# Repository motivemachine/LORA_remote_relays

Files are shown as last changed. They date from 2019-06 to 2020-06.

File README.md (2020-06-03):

# Lora Remote Relays

AC powered relay control board using Lora radios. Turn on lights, heaters or anything else you need at a distance.
The first one has been installed and running smooth for several months now! Check it out here: https://asthemillturns.serveblog.net/lora-ac-relays.html

## Notice about AC and relays!
##### Build at your own risk.
This devices runs on 110VAC, and controls other 110VAC devices. Do not make this if you don't know what you're doing! Power traces are very conservatively rated at 8 amp total (both relays combined), further changes and testing should increase this. There is no snubber circuity on the relays, so as-is should only be used with resistive loads (lights, heaters, etc.). Small fans should be fine. Running motors should have proper circuitry in place on the relay outputs to handle any noise or back-EMF from such devices.

## Project status
Board design and code for v1.1 is completed and all is running well. Board v1.2 design is complete but code has not been written yet. Code for v1.1 should work almost as-is after changing the pin numbers. Primarily the difference between 1.1 and 1.2 is that 1.1 must poll the radio for new packets while the new version will use interrupts. Other changes are improved silkscreening and more IO breakouts for other projects.

## Pinout description

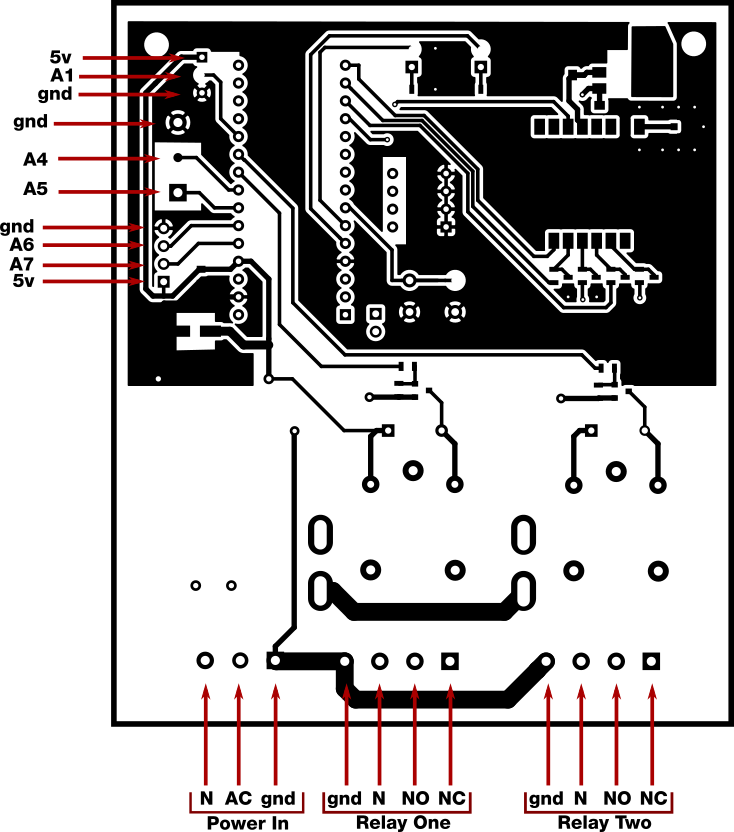
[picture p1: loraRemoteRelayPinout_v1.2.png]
Pinouts


I've broken out some extra arduino pins for integration in future projects. Starting from the upper left:
  * The first three pins from upper-left down are 5 volts, Analog 1, and ground. This was originally used for a TMP36 analog temperature sensor. This would also work with any of the Dallas One-wire digital temperature sensors.
  * Next we have a terminal block with Ground, analog 4 and analog 5. My purpose for these is to include some external on/off switches for the relays. Could be handy to turn the lights on manually when already standing next to them. The terminal block
  * Final four pins are ground, analog 6, analog 7, and 5 volts. These are just for future projects and could be used for more external sensors, switches, or status LEDs
  * To the lower right of the Nano the serial pins are exposed for future ideas.

## Completed board
This is a photo of the complete v1.1 board. The schematics are up to date with v1.2, which adds some extra IO pins, adjusted silkscreen, and moved some parts to make them easier to work with (like moving the fuse holder farther away from the relays)
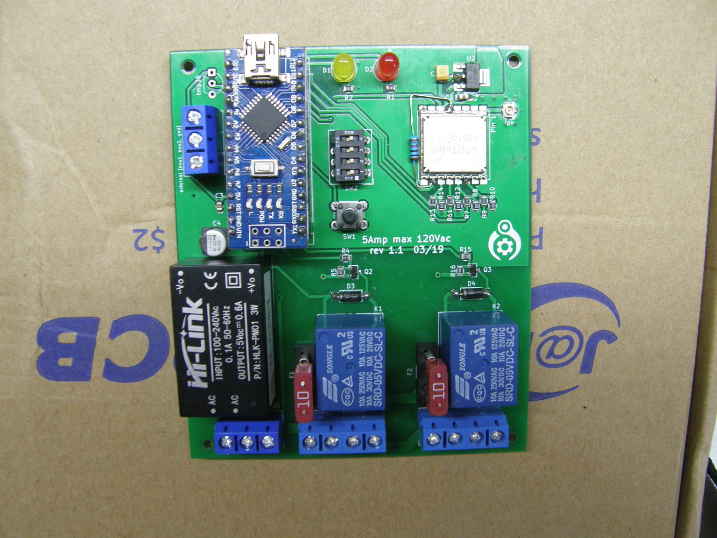
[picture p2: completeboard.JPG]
Completed 1.1 board


## Usage/code description
There are two PlatformIO project folders, one for the main program, one named 'circuit test'. The circuit test routing just verifies everything was connected correctly: blink leds, toggle relays, send a packet. Both programs are contained in the 'src/' folder and can be pulled from there if you wish to use the code with Arduino IDE.

Some of these software functions are in a state of change as I figure out how best to integrate these devices with my Lora home network, but the basic purpose remains the same:
  * Set local(self) and destination radio addresses (in the form of a byte in Hex format)
      * Destination address is read from the dip switches on startup. Simply make sure these are the same across all boards. In this case it is the address of the Lora radio on the Raspberry Pi that controls everything.
      * If the button is held on startup (or while the arduino nano reset button is pressed) blink the LEDs while in the 'set local address' function. Set the dip switches *different* on each board so each one can be uniquely addressed by whatever device you have turning the relays on and off. Press button again to write this new address to EEPROM.
  * Receive message on which relay to turn on or off
    * Currently this just listens for a message to the local address and a 2 index array of zeros and ones (i.e [1,0]). First element is what the first relay state should be, second is what the second relay state should be.
  * Reply with ACK after processing the previous message, or respond with current relay states when asked
    * This isn't quite complete yet but the plan is to implement a proper ack/nack response for more reliable operation.
    * The second thing is to reply to the message 'STAT' with the current status of both relays. The thinking is any one control device may turn the relays on and off, but it would be nice of other control devices could later know what their status is without toggling anything on or off. This also lets a controller know that a specific board is, in fact, online and reachable.

## TODO

- [ ] Create and upload a proper BOM
- [x] Finish and debug 'status' functions
- [ ] Further testing of board temperature rise at high currents
- [ ] Change from polling loop to pin-change interrupt
- [x] Clean up lots of old comments, debug info and test functions
- [x] Add watchdog timer for protection from random hangups.

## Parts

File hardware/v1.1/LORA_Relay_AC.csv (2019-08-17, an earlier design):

Source: | /home/cale/CAD/Kicad/LORA_Relay_AC/LORA_Relay_AC.sch
Date: | Tue 19 Mar 2019 10:45:48 AM MDT
Tool: | Eeschema 5.0.2-bee76a0~70~ubuntu16.04.1
Generator: | /usr/share/kicad/plugins/bom_csv_grouped_by_value_with_fp.py
Component Count: | 44
Ref | Qnty | Value | Cmp name | Footprint | Description | Vendor
C1, | 1 | 1uf | C_Small | Capacitors_SMD:C_0805_HandSoldering | Unpolarized capacitor, small symbol
C2, | 1 | 22uf | C_Small | Capacitors_SMD:C_0805_HandSoldering | Unpolarized capacitor, small symbol
C3, | 1 | .1uf | C | Capacitors_SMD:C_0805 | Unpolarized capacitor
C4, | 1 | 100uf | CP | Capacitors_SMD:CP_Elec_5x5.3 | Polarized capacitor
D1, D2, | 2 | LED | LED | LEDs:LED_D5.0mm | Light emitting diode
D3, D4, | 2 | 4001 | D | Diodes_THT:D_A-405_P7.62mm_Horizontal | Diode
F2, F1, | 2 | Fuse | Fuse | Fuse_Holders_and_Fuses:BladeFuse-Mini | Fuse
H1, H2, H3, H4, | 4 | MountingHole | MountingHole | Mounting_Holes:MountingHole_2.5mm | Mounting Hole without connection
J1, | 1 | ACin | Screw_Terminal_01x03 | TerminalBlocks_Phoenix:TerminalBlock_Phoenix_MKDS1.5-3pol | Generic screw terminal, single row, 01x03, script generated (kicad-library-utils/schlib/autogen/connector/)
J2, | 1 | relay1 | Conn_01x04 | TerminalBlocks_Phoenix:TerminalBlock_Phoenix_MKDS1.5-4pol | Generic connector, single row, 01x04, script generated (kicad-library-utils/schlib/autogen/connector/)
J3, | 1 | IPX | Conn_Coaxial | Connectors_Molex:Molex_Microcoaxial_RF | coaxial connector (BNC, SMA, SMB, SMC, Cinch/RCA, ...)
J5, | 1 | relay2 | Conn_01x04 | TerminalBlocks_Phoenix:TerminalBlock_Phoenix_MKDS1.5-4pol | Generic connector, single row, 01x04, script generated (kicad-library-utils/schlib/autogen/connector/)
J7, | 1 | tmp36 | Conn_01x03 | TO_SOT_Packages_THT:TO-92_Inline_Wide | Generic connector, single row, 01x03, script generated (kicad-library-utils/schlib/autogen/connector/)
J8, | 1 | external_Sw | Screw_Terminal_01x03 | TerminalBlocks_Phoenix:TerminalBlock_Phoenix_MKDS1.5-3pol | Generic screw terminal, single row, 01x03, script generated (kicad-library-utils/schlib/autogen/connector/)
K1, | 1 | relay1 | FINDER-32.21-x000 | Relays_THT:Relay_SPDT_SANYOU_SRD_Series_Form_C | FINDER 32.21-x000, Single Pole Relay, 6A
K2, | 1 | relay2 | FINDER-32.21-x000 | Relays_THT:Relay_SPDT_SANYOU_SRD_Series_Form_C | FINDER 32.21-x000, Single Pole Relay, 6A
Q3, Q2, | 2 | MMBT3904 | MMBT3904 | TO_SOT_Packages_SMD:SOT-23 | 0.2A Ic, 40V Vce, Small Signal NPN Transistor, SOT-23
R1, R2, | 2 | 3k3 | R | Resistors_SMD:R_0805 | Resistor
R5, R16, | 2 | 10k | R | Resistors_SMD:R_0805 | Resistor
R9, R7, R13, R11, | 4 | 1k | R_Small | Resistors_SMD:R_0805 | Resistor, small symbol
R10, R8, R14, R12, | 4 | 2k | R_Small | Resistors_SMD:R_0805 | Resistor, small symbol
R15, R4, | 2 | 100 | R | Resistors_SMD:R_0805 | Resistor
SW1, | 1 | SW_Push | SW_Push | Buttons_Switches_THT:SW_PUSH_6mm_h4.3mm | Push button switch, generic, two pins
SW2, | 1 | SW_DIP_x04 | SW_DIP_x04 | Buttons_Switches_THT:SW_DIP_x4_W7.62mm_Slide | 4x DIP Switch, Single Pole Single Throw (SPST) switch, small symbol
U1, | 1 | HLK-PM01 | HLK-PM01 | MainWorking:HLK-PM01 | AC-DC 220V-5V power module
U2, | 1 | AMS1117-3.3 | AMS1117-3.3 | TO_SOT_Packages_SMD:SOT-223-3_TabPin2 | 1A Low Dropout regulator, positive, 3.3V fixed output, SOT-223
U3, | 1 | ArduinoNano | ArduinoNano | MainWorking:ArduinoNano
U4, | 1 | Sx1278_LORA_Module | Sx1278_LORA_Module-MainWorking | MainWorking:LORA_SX1278_Module

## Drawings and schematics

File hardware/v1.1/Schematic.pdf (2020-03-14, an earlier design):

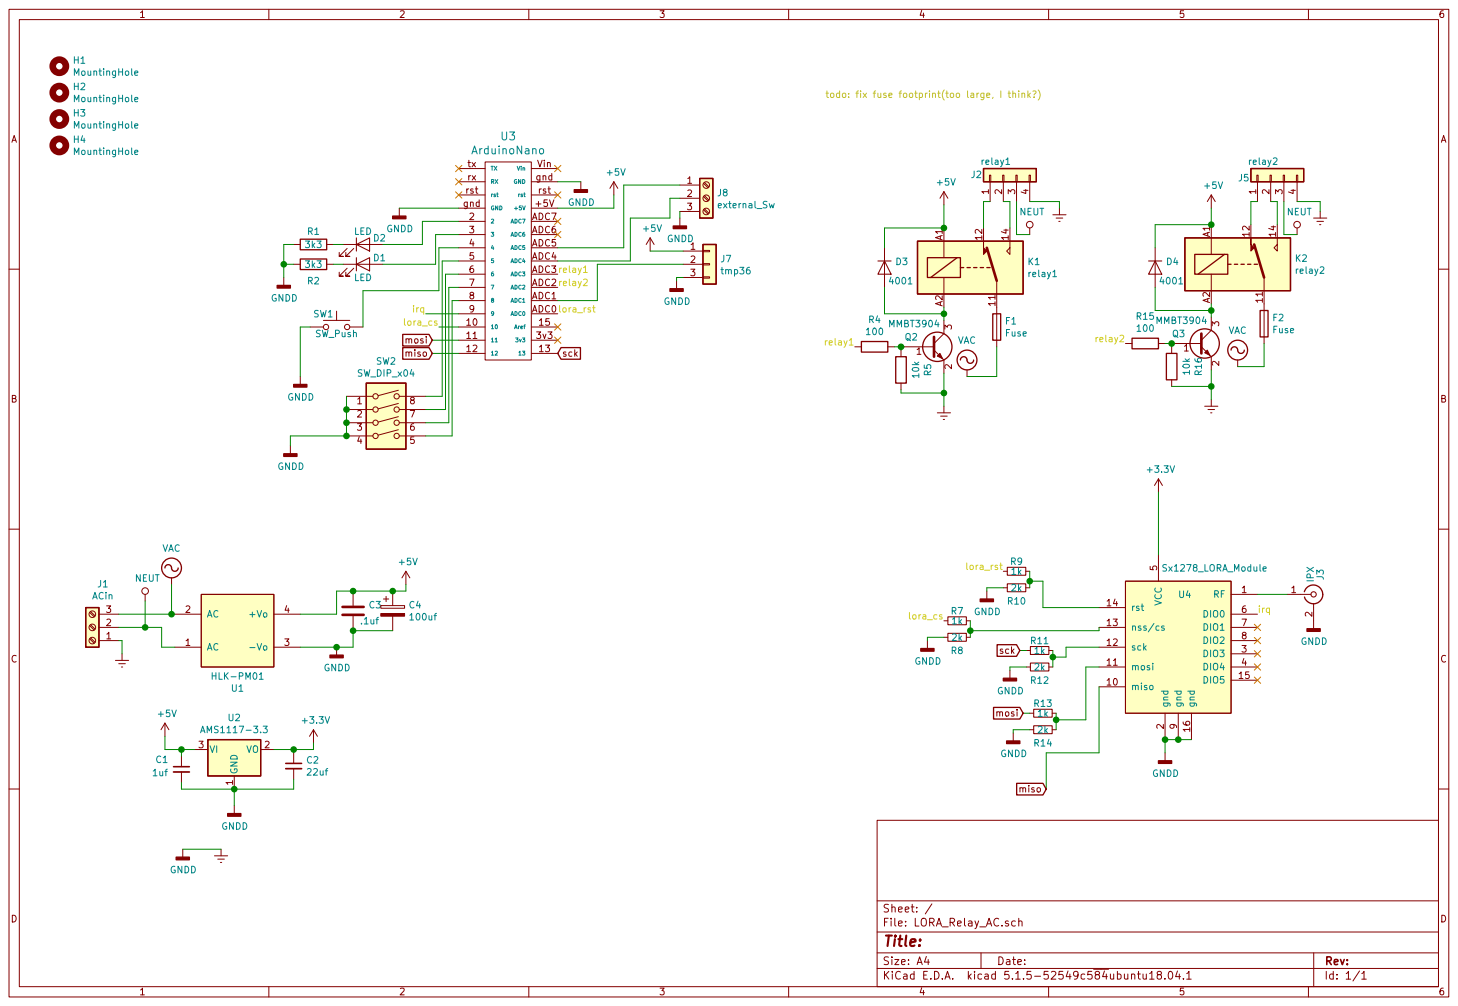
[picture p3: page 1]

todo: fix fuse footprint(too large, I think?)

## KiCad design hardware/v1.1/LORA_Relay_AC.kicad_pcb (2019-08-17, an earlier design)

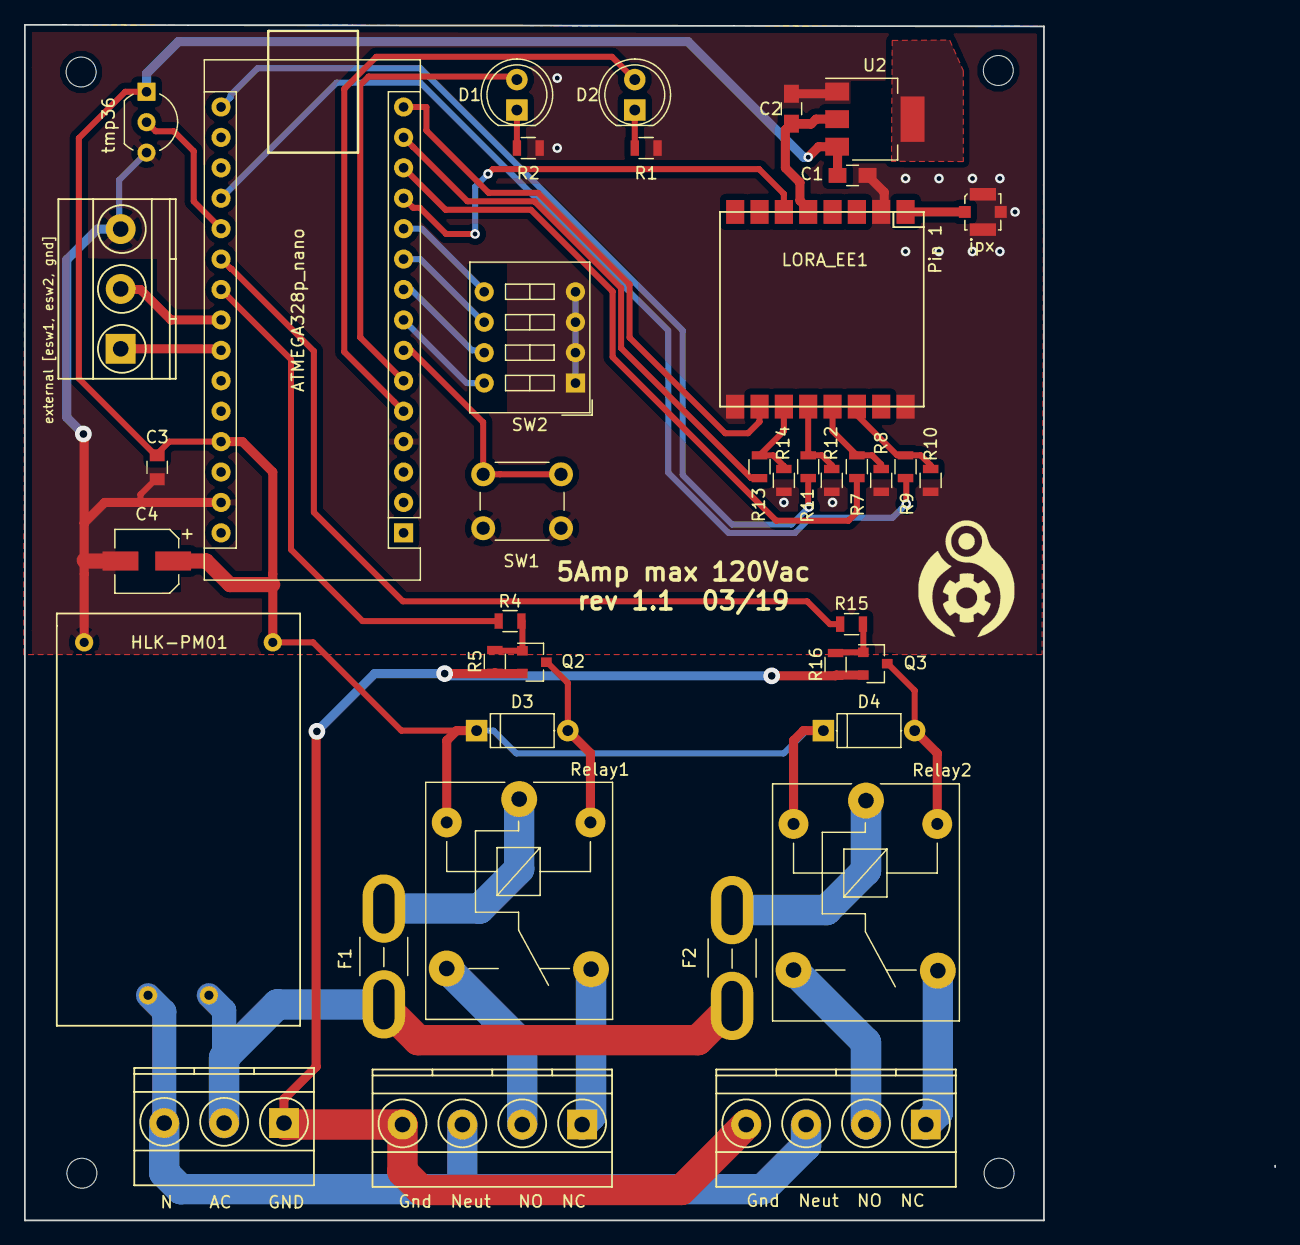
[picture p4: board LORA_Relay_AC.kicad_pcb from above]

Board: 2 copper layers, 85.1 x 99.8 mm, 44 parts (0 on the bottom side), 41 nets.

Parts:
ATMEGA328p_nano: ArduinoNano
C1: 1uf; C_0805_HandSoldering
C2: 22uf; C_0805_HandSoldering
C3: .1uf; C_0805
C4: 100uf; CP_Elec_5x5.3
D1, D2: LED; LED_D5.0mm
D3, D4: 4001; D_A-405_P7.62mm_Horizontal
F1, F2: Fuse; BladeFuse-Mini
Gnd  Neut   NO  NC: relay1; TerminalBlock_Phoenix_MKDS1.5-4pol
Gnd  Neut  NO  NC: relay2; TerminalBlock_Phoenix_MKDS1.5-4pol
H1, H2, H3, H4: MountingHole; MountingHole_2.5mm
HLK-PM01: HLK-PM01
LORA_EE1: Sx1278_LORA_Module; LORA_SX1278_Module
N    AC    GND: ACin; TerminalBlock_Phoenix_MKDS1.5-3pol
Q2, Q3: MMBT3904; SOT-23
R1, R2: 3k3; R_0805
R4, R15: 100; R_0805
R5, R16: 10k; R_0805
R7, R9, R11, R13: 1k; R_0805
R8, R10, R12, R14: 2k; R_0805
Relay1: relay1; Relay_SPDT_SANYOU_SRD_Series_Form_C
Relay2: relay2; Relay_SPDT_SANYOU_SRD_Series_Form_C
SW1: SW_Push; SW_PUSH_6mm_h4.3mm
SW2: SW_DIP_x04; SW_DIP_x4_W7.62mm_Slide
U2: AMS1117-3.3; SOT-223-3_TabPin2
external [esw1, esw2, gnd]: external_Sw; TerminalBlock_Phoenix_MKDS1.5-3pol
ipx: sma; Molex_Microcoaxial_RF
tmp36: tmp36; TO-92_Inline_Wide

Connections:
+3V3: C2.1, LORA_EE1.5, U2.2
+5V: ATMEGA328p_nano.+5V, C1.1, C3.1, C4.1, D3.1, D4.1, HLK-PM01.4, Relay1.A1, Relay2.A1, U2.3, tmp36.1
/irq: ATMEGA328p_nano.9, LORA_EE1.6
/lora_cs: ATMEGA328p_nano.10, R7.2
/lora_rst: ATMEGA328p_nano.ADC0, R9.2
/relay1: ATMEGA328p_nano.ADC3, R4.2
/relay2: ATMEGA328p_nano.ADC2, R15.2
Earth: Gnd Neut NO NC.4, Gnd Neut NO NC.4, N AC GND.1, Q2.2, Q3.2, R5.1, R16.1
GNDD: ATMEGA328p_nano.gnd, C1.2, C2.2, C3.2, C4.2, HLK-PM01.3, LORA_EE1.2, LORA_EE1.9, LORA_EE1.16, R1.2, R2.2, R8.2, R10.2, R12.2, R14.2, SW1.1, SW2.1, SW2.2, SW2.3, SW2.4, U2.1, external [esw1, esw2, gnd].3, ipx.2, tmp36.3
NEUT: Gnd Neut NO NC.3, Gnd Neut NO NC.3, HLK-PM01.1, N AC GND.2
unnamed: D1.1, R2.1
unnamed: ATMEGA328p_nano.3, D1.2
unnamed: D2.1, R1.1
unnamed: ATMEGA328p_nano.2, D2.2
unnamed: D3.2, Q2.3, Relay1.A2
unnamed: D4.2, Q3.3, Relay2.A2
unnamed: F1.1, Relay1.11
unnamed: F2.1, Relay2.11
unnamed: Gnd Neut NO NC.1, Relay1.12
unnamed: Gnd Neut NO NC.2, Relay1.14
unnamed: LORA_EE1.1, ipx.1
unnamed: Gnd Neut NO NC.1, Relay2.12
unnamed: Gnd Neut NO NC.2, Relay2.14
unnamed: ATMEGA328p_nano.ADC1, tmp36.2
unnamed: ATMEGA328p_nano.ADC5, external [esw1, esw2, gnd].1
unnamed: ATMEGA328p_nano.ADC4, external [esw1, esw2, gnd].2
unnamed: Q2.1, R4.1, R5.2
unnamed: Q3.1, R15.1, R16.2
unnamed: LORA_EE1.13, R7.1, R8.1
unnamed: LORA_EE1.14, R9.1, R10.1
unnamed: LORA_EE1.12, R11.1, R12.1
unnamed: LORA_EE1.11, R13.1, R14.1
unnamed: ATMEGA328p_nano.4, SW1.2
unnamed: ATMEGA328p_nano.8, SW2.5
unnamed: ATMEGA328p_nano.7, SW2.6
unnamed: ATMEGA328p_nano.6, SW2.7
unnamed: ATMEGA328p_nano.5, SW2.8
VAC: F1.2, F2.2, HLK-PM01.2, N AC GND.3
miso: ATMEGA328p_nano.12, LORA_EE1.10
mosi: ATMEGA328p_nano.11, R13.2
sck: ATMEGA328p_nano.13, R11.2

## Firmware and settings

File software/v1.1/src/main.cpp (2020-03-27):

#include <Arduino.h>
#include <SPI.h>
#include <LoRa.h>
#include <EEPROM.h>

// ####### TODO  #######//
// add IRQ pin-change interrupt function instead of polling the radio. for v1.1 boards this will have to be tested as a pin-CHANGE interrupt. v1.2 boards will have the IRQ pin attached to D2

#define csPin 10
#define resetPin A0
//#define irqPin 9 //This is not an ATMEGA external interrupt, and will probably be handled manually with a pulldown resistor and a pin-change interrupt

#define ledOne 3
#define ledTwo 2
#define button 4    //the on-board push switch, for debugging and setting local device address
#define relayOne A3
#define relayTwo A2
#define temp     A1  // Optional TMP36 analog temperature sensor. This pin will also work with Dallas 1-Wire sensors

// These are the jumper pins for address selecting
#define jumpone   5
#define jumptwo   6
#define jumpthree 7
#define jumpfour  8

#define extOne A5      //pins for external switches. Switch press is digital pin LOW
#define extTwo A4

byte switchArray[4];
byte relayStates[2] = {0,0};  //holds the on/off status of both relays
int packetLength;
byte localAddress = 0x15; //20 Will hardcode this for now, will determine from jumper/dip switches later
byte destAddress = 0x25; //37. 0xFF is standard LoRa broadcast address

int beatdelaytime = 1000;
long beatdelay;

//These are keyword arrays, to be parsed in from the radio and be acted on
char statCall[4] = {'S','T','A','T'};

void sayStatus(byte dest) //Function to update current relay status
{
  LoRa.beginPacket();
  LoRa.write(dest);
  LoRa.write(localAddress);
  LoRa.write(1);
  LoRa.write(5);//temporarily making oversized        // relayStates is a 2 index array
  LoRa.print("STAT");
  LoRa.print(relayStates[0]);
  LoRa.print(relayStates[1]); // send stat and then the states, to let the bridge receiver know this is a stat message right off the bat
  LoRa.endPacket();
  //LoRa.receive();
}

void Receive(int packetSize)
{
  if (packetSize == 0) return;
  int i = 0;
  int recipient = LoRa.read();
  if (recipient != localAddress) return;
  byte sender = LoRa.read();
  byte incomingMsgId = LoRa.read();
  byte incomingLength = LoRa.read();

  char incomingArray[incomingLength];
  while (LoRa.available())
  {
    incomingArray[i] = (char)LoRa.read();
    i++;
  }
  if (incomingLength == 2) // assume two index arrays are the boolean values to set the relays
  {
    //Serial.println(String(incomingArray[0], DEC));
    //Serial.println(incomingArray[1]);
    relayStates[0] = (byte(incomingArray[0]) - 48);  //subtract the ASCII value of '0' to convert to actual int Zero.
    relayStates[1] = (byte(incomingArray[1]) - 48);
    //changeStates = true;
    if (relayStates[0] != 0) relayStates[0] = 1; // make sure array inputs are sensible
    if (relayStates[1] != 0) relayStates[1] = 1;
    digitalWrite(relayOne, relayStates[0]);
    digitalWrite(ledOne, relayStates[0]);
    digitalWrite(relayTwo, relayStates[1]);
    digitalWrite(ledTwo, relayStates[1]);
    LoRa.receive();
    //return;
    }
    else // message must not be changing relay states. Convert to strings and look for keywords
    { // not yet finished
      return;
      //if ((statCall[0] == incomingArray[0]) && (statCall[1] == incomingArray[1]) && (statCall[2] == incomingArray[2]) && (statCall[3] == incomingArray[3])) //this needs to be changed to strncmp asap
      //{
        //Serial.println(F("got status request"));
        //delay(600);       // long delay to let requester switch back to tx mode, will be shorter later after testing (now trying 200, down from 1000)
        //sayStatus(sender); // send status message to the address the 'STAT' request came from
      //}
    }
  //for (int t = 0; t < incomingLength; t++) // debug function. prints received array
  //{
    //Serial.print(incomingArray[t]);
  //}
}

void setDestaddr()   // function to set destination address. When used, runs every time on startup
{
  //Serial.println("set destination address");
  int j = 0;
  for (int i = 5; i < 9; i++) {  //iterate through switchArray and populate with DIP switch reads (pins 5, 6, 7, 8)
  switchArray[j] = digitalRead(i);
  j++;
}
destAddress = (switchArray[0]*1)+(switchArray[1]*2)+(switchArray[2]*4)+(switchArray[3]*8); //convert binary array to decimal address
destAddress += 37;
//Serial.print("New destination address: "); Serial.println(destAddress);
}

void setLocaladdr()  //function to set device address. Press and hold push switch when turning-on to enter this function. Set device address with DIP switches while LED is fading, then press again to set address.
{
//Serial.println("Set device address");
  do
  { //fade LED until button is pressed
    for (int k = 255; k > 0; k -=10)
    {
      analogWrite(ledOne, k);
      delay(10);
    }
    for (int k = 0; k< 255; k += 10)
    {
      analogWrite(ledOne, k);
      delay(10);
    }
  } while(digitalRead(button)); // continue this loop until button is pressed again.
digitalWrite(ledTwo, LOW);
delay(55);
digitalWrite(ledTwo, HIGH);
delay(55);
digitalWrite(ledTwo, LOW);
int newAddr;
int j = 0;
for (int i = 5; i < 9; i++) {  //iterate through swithArray and populate with DIP switch reads (pins 5, 6, 7, 8)
  switchArray[j] = digitalRead(i);
  j++;
}
newAddr = (switchArray[0]*1)+(switchArray[1]*2)+(switchArray[2]*4)+(switchArray[3]*8); //convert binary array to decimal address
newAddr += 40;
//Serial.print("New local address is"); Serial.println(newAddr);
EEPROM.write(1, newAddr);
}

void setup()
{
  //Serial.begin(9600);
  //Serial.println("Starting up");

  LoRa.setPins(csPin, resetPin);
  //Address select dip switches
  pinMode(jumpone, INPUT_PULLUP);
  pinMode(jumptwo, INPUT_PULLUP);
  pinMode(jumpthree, INPUT_PULLUP);
  pinMode(jumpfour, INPUT_PULLUP);

if (!LoRa.begin(430E6))
  {
    while (1)
    {
      digitalWrite(ledOne, HIGH);
      delay(80);
      digitalWrite(ledOne, LOW);
      delay(80);
    }
  }

  //detachInterrupt(digitalPinToInterrupt(2)); //turn off that lora interrupt flag, we're not using it.

  pinMode(ledOne, OUTPUT);
  pinMode(ledTwo, OUTPUT);
  pinMode(button, INPUT_PULLUP);
  pinMode(relayOne, OUTPUT);
  pinMode(relayTwo, OUTPUT);
  digitalWrite(relayOne, relayStates[0]);
  digitalWrite(relayTwo, relayStates[1]);
  //pinMode(temp, INPUT);
  pinMode(extOne, INPUT_PULLUP);
  pinMode(extTwo, INPUT_PULLUP);

  //setDestaddr();  //set destination address from the 4 dip switches
  if (digitalRead(button) == LOW){setLocaladdr();} //hold button on startup to enter this function. Set desired local address with DIP switches. Press button again to save new address

  digitalWrite(ledOne, HIGH);
  digitalWrite(ledTwo, HIGH);
  delay(1000);
  digitalWrite(ledOne, LOW);
  digitalWrite(ledTwo, LOW);
  localAddress = EEPROM.read(1); //read previously stored local address
  //localAddress = 0x14; //20

  sayStatus(destAddress); //send a status update to the home receiver when powered up
  //Serial.println("starting up");
  LoRa.setTxPower(10); //was 14
  delay(200);
  LoRa.receive();
  beatdelay = millis();
}

void loop()
{
  if (digitalRead(button) == LOW)
  {
    //Serial.println("sending");
    sayStatus(0x25);
    delay(400);
  }

  if (millis() - beatdelay > beatdelaytime) { // blink the #2 led as a heartbeat. For debugging it's problem with randomly hanging after about 4+ hours
    digitalWrite(ledTwo, !digitalRead(ledTwo));
    beatdelay = millis();
  }
  //poll continuously for new packets, calling for a return of packet size and running if it's > 0
  packetLength = LoRa.parsePacket();
  if (packetLength){Receive(packetLength);}
  if (!digitalRead(extOne)) //poll external switch for relay 1 button press
  {
    digitalWrite(relayOne, !digitalRead(relayOne));

    relayStates[0] = !relayStates[0];               // toggle relay setting and update states array
    digitalWrite(ledOne, relayStates[0]);
    delay(300);    // debounce delay
    // put a function here that declares the states
  }
  if (!digitalRead(extTwo)) // poll external switch for relay 2 button pressed
  {
    digitalWrite(relayTwo, !digitalRead(relayTwo));
    relayStates[1] = !relayStates[1];              // toggle relay setting and update status array
    digitalWrite(ledTwo, relayStates[1]);
    delay(300);
  }
}

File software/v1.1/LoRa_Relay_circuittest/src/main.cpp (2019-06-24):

#include <Arduino.h>
#include <SPI.h>
#include <LoRa.h>

#define ledOne 3
#define ledTwo 2
#define testSw 4
#define relayOne A3
#define relayTwo A2
#define temp     A1
#define eswOne   A5
#define eswTwo   A4

const int csPin = 10;          // LoRa radio chip select
const int resetPin = A0;       // LoRa radio reset
const int irqPin = 9;         // This is not an interrupt. Radio must be polled for new packets

byte msgCount = 0;
byte localAddress = 0x14;    //20
byte destination = 0x25;

bool status[2] = {false, false};

void setup()
{
  Serial.begin(9600);
  pinMode(ledOne, OUTPUT);
  pinMode(ledTwo, OUTPUT);
  pinMode(testSw, INPUT_PULLUP);
  pinMode(relayOne, OUTPUT);
  pinMode(relayTwo, OUTPUT);
  pinMode(temp, INPUT);
  pinMode(eswOne, INPUT_PULLUP);
  pinMode(eswTwo, INPUT_PULLUP);

  Serial.println("pin setup complete");

  LoRa.setPins(csPin, resetPin, irqPin);
  if (!LoRa.begin(430E6))
  {
      Serial.println("Starting LoRa failed!");
      while (1);
  }
  Serial.println("Radio ready!");
}

void loop()
{
    Serial.println("Running");
    digitalWrite(relayTwo, LOW);
    digitalWrite(ledOne, HIGH);
    delay(500);
    digitalWrite(ledTwo, HIGH);
    digitalWrite(ledOne, LOW);
    delay(500);
    digitalWrite(ledTwo, LOW);
    digitalWrite(relayOne, HIGH);
    delay(500);
    digitalWrite(relayOne, LOW);
    digitalWrite(relayTwo, HIGH);
    delay(500);
}

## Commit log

2019-06-24 upload kicad and gerbers
    [LORA_Relay_AC-B.Cu.gbr, LORA_Relay_AC-B.Mask.gbr, LORA_Relay_AC-B.SilkS.gbr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]
2019-06-24 upload circuit test program
2019-08-17 rework 1.1 code, add more docs
    [LORA_Relay_AC-B.Cu.gbr, LORA_Relay_AC-B.Mask.gbr, LORA_Relay_AC-B.SilkS.gbr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]
2020-03-13 add watchdog timer fallback
2020-03-14 fixed watchdog mistake, fixing SPI issues
    [main.cpp]
